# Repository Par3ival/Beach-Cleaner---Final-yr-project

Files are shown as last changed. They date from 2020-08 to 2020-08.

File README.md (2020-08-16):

# Beach-Cleaner---Final-yr-project

This documents all the work put towards the final year group project (6 People).

I ended up doing all the work towards: machine vision, machine learning, creating neural nets, ROS, inter robot communication techniques, message formats, prototype/final product CAD designs and small scale PCB designs.
The rest of the work was mostly worked on by 3 of my team mates: Oly Pope, Jack White and Stephen Jeranyama. With Leo Garroch contributing to LED sequence detection.

THIS IS A CLONED REPO OF ALL WORK CARRIED OUT.

For access to the full Catkin_WS see this link to Google Drive (GitHub hates me!)

--->[ROS BUILD - HOSTED ON DRIVE](https://drive.google.com/drive/folders/1dpi-4POSFZ2x0RheGSwLuPaQL2tJi76T?usp=sharing)<---

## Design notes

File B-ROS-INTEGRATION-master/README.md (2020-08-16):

# B-ROS-INTEGRATION

https://github.com/tue-robotics/cb_base_navigation
`--- Example for nav stack use ---`

https://github.com/abhineet123/ORB_SLAM2 
`--- Example for 2D map for ORBSLAM ---`
# SETTING UP NEW CAMERAS FOR STEREO
This includes if cameras arent changed but their separation is

``rosrun camera_calibration cameracalibrator.py --approximate 1 --size 6x4 --square 0.12 right:=/cam_R/usb_camR/image_raw left:=/cam_L/usb_camL/image_raw left_camera:=/cam_L/usb_camL right_camera:=/cam_R/usb_camR``

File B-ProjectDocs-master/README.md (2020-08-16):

# B-ProjectDocs

#### This repository will demonstrate the design and implemention of a system capable of fulfilling autonomous navigation of a beach and cleaning plastics.  

## Key links  

* [The Buoys Portfolio](https://thebeachbuoys.wordpress.com)

* [ROS Intergration](https://github.com/lboroWMEME-19WSD001/B-ROS-INTEGRATION)

* [CAD designs](https://github.com/lboroWMEME-19WSD001/B-CAD/tree/master/DESIGNS)

* [Idea testing](https://github.com/lboroWMEME-19WSD001/B-Idea-Testing)

* [Identify recycling bins from optically coded sensors](https://github.com/lboroWMEME-19WSD001/B-Idea-Testing/tree/master/LedDetecting)

* [Identify different types of rubbish](https://github.com/lboroWMEME-19WSD001/B-Idea-Testing/tree/master/Deep%20Learning)

* [Identify and alert operators about other wildlife](https://github.com/lboroWMEME-19WSD001/B-ProjectDocs/tree/master/Wildlife%20Alert)

* [Identify waterline and actively avoid or mitigate against the incoming tide](https://github.com/lboroWMEME-19WSD001/B-Idea-Testing/tree/master/Tide_Detection)

## File structure 
**Folders:** Example-Folder

**Files:** example-file

**Read me files:** README.md

The only file in B-ProjectDocs should be README.md, the rest should be folders.

Comments when committing in description box: "+" for changes added "-" for changes removed.

e.g. + added file structure changes

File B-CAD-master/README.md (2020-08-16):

# B-CAD
All cad designs for modelling and printing

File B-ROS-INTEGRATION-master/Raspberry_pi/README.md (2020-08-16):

# Information on coding a Rapberry Pi will go here

## Downloading libraries
Downloading pip: `$ sudo apt install python-pip`

Downlaoding packages: `$ pip install [library name]` 

Check the package is available [here](https://pypi.org/)

## GPIO pinout
https://www.raspberrypi.org/documentation/usage/gpio/

## ROS_SPI and bb_SPI

These two programs were created in conjunction with oneanother to allow for the communication between a raspberry Pi and botboarduino/arduino. This has allowed for full remote control through ROS by subscribing to a topic on the PI, mapping the data and then transmitting over SPI for the aruduino (SPI slave) to recieve and then interpret to turn into movement commands.

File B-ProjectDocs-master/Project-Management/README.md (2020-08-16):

# Weekly tasks will be assigned here 

## 10/02/2020

**Leo:** make some mbed code for actual bin patterns, then video it

## 03/02/2020

**Leo:** Make progress on bin detection code for monday

## 27/01/20

**Oly:** Labview and ROS intergration.

**Dan:** Navigation.

**Jack:** Design tri track top and bottom plate.

**Stephen:** Create a subscriber for Arduio wifi data recieveing (UDP).

**Leo:** Tide detection.

**Iffy:** Continue with mapping.

## 20/01/20

**Jack:** Design a top for the tri track for all the electronics and create a data processing flow chart.

**Dan:** Work on navigation for the robot.

**Leo:** Map for what messages are bring sent.

**Iffy:** Continue with mapping.

**Stephen:** Create a subscriber for Arduio wifi data recieveing (UDP).

## 07/01/20
**Leo:** Produce 20s Vid of code development, continue to develop tide detection technology

**Jack:** Produce 20s Vid of arm development, edit GW2 video and continue to improve collection technology

**Stephen:** Produce 20s Vid of code development, continue to assess integration between ROS and sub-systems

**Oly:** Produce 20s Vid of code development, continue to improve sound response system and complete plan on page

**Ify:** Produce 20s Vid of code development, continue to develop path finding work

**Dan:** Produce 20s Vid of code development, continue work on template matching

## 02/12/19
**Leo:** Tide detection: sensor eval/research, for arduino.

**Jack:** Put holes in lazer cut wood and continue to build arm. Design mounting for cameras and arduino for eye in the sky.

**Stephen:** Global timer for ROS, create a subscriber to get co-ordinates.

**Oly:** Photogramatory for myrio FPGA + seagull sounds + look at labview/ROS intergration

**Ify:** Route planning.

**Dan:** Psudo code for crab tracking and PCB for power supply.

## 25/11/19

**Leo:** Tide detection: sensor eval/research, for arduino.

**Jack:** Put holes in lazer cut wood and continue to build arm. Design mounting for cameras and arduino for eye in the sky.

**Stephen:** Global timer for ROS, create a subscriber to get co-ordinates.

**Oly:** Photogramatory for myrio FPGA + seagull sounds + look at labview/ROS intergration

**Ify:** Route planning.

**Dan:** Psudo code for crab tracking and PCB for power supply.

## 18/11/19

**Dan:** Psudo code for crab tracking and PCB for power supply.

**Oly:** Photogramatory for myrio FPGA + seagull sounds.

**Stephen:** Global timer for ROS, create a subscriber to get co-ordinates and Gazebo.

**Ify:** Route planning.

**Leo:** Identify coloured lights in a video and send data to analyse.

**Jack:** Servo arm and camera mounts.

## 11/11/19

**Leo:** Formatting data to compare with pattern data and write pattern data.

**Jack:** 

stage 1: design arm for robot and draw on CAD.

stage 2: build robot arm and mount to rover.

stage 3: integrate with microcontroller and get bot to work.

**Oly:** Myrio experiments.

**Stephen:** Setting up nodes for ROS and node diagram.

**Ify:** Route planning.

## 04/11/19 - 11/11/19

**Jack:** Designing robot arm and drawing in CAD 

**Leo:** LED indentifying code to work with video and pattern recognition.

**Stephen:** ROS node map.

**Dan:** Machine visin for tracking crabs.

**Oly:** How to detect seagull sound with labVIEW, prepare documents for PST, LabView with myRio.

## 28/10/19 - 04/11/19

**Dan + Leo:** Research on wireless communication, and wireless adapters.

**Leo:** Function to identify LEDs from a picture in simulink or python.

**Stephen + Jack:** ROS.

**Stephen + Oly:**  How to filter microplastics.

**Ify:** LabVEIW.

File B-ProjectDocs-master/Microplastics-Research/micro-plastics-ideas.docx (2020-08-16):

# Requirements

- Filter micro plastics larger than sand
- Automated robot system
- Keep track of areas where sand has been collected
- Collect sand underwater? Adds, complexity

# Filtering techniques

- Electrostatic mesh - https://youtu.be/00Qw36ooUp4
  - https://youtu.be/nfMGrq8W5rI
- Moving mesh filter - https://youtu.be/sHnqjKwVND0

# Robot ideas

- Mini excavators - https://youtu.be/FQZZBF3viI4
  - https://youtu.be/69Gaw0k65qQ
  - https://youtu.be/j4845zwMVBs
- Underwater robot - https://youtu.be/6pBH-3lXXO0

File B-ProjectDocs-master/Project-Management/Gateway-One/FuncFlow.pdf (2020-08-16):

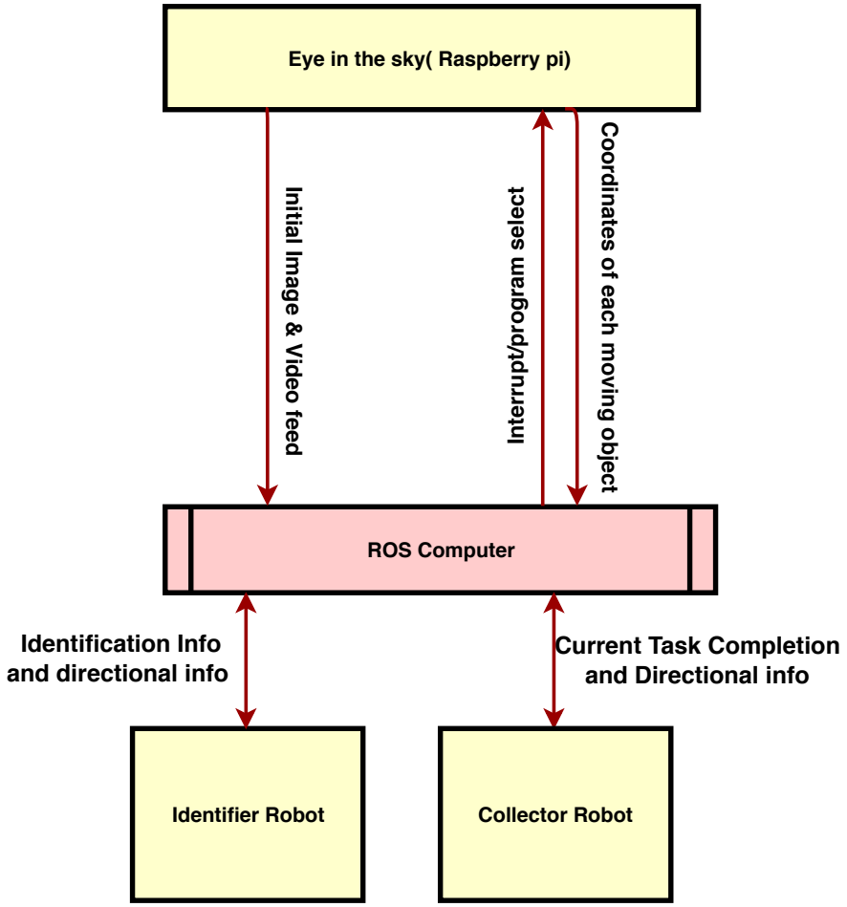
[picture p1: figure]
Eye in the sky( Raspberry pi); ROS Computer; Interrupt/program select; Coordinates of each moving object; Identification Info and directional info; Current Task Completion and Directional info; Collector Robot

# Identifier Robot Initial Image & Video feed

# Flow Diagram of the Main Idea

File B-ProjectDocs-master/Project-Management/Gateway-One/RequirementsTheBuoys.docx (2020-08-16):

# Group Project Systems Approach

# Introduction

Aim: Utilise integrated autonomous technologies to enhance and develop waste management in coastal areas

Objectives:

- Integration of several individual systems to produce a more complex system of systems, capable of delivering user specified tasks
- Automation of whole system to minimise human interactions
- Effective and comprehensive movement of different materials to specified areas

# Requirements Specification

## Navigation and mapping

Description

The system will map objects’ locations and the position of the tide. This information will be used to task sub-systems and determine routes for them to travel.

Stimulus/Response Sequences

Objects on the surface will be detected and their coordinates noted. A sub system will then receive these coordinates and move to that position, avoiding any potential hazards. This process will be utilized again when the type of material has been determined and the sub system will move to its designated bin.

Functional Requirements

NM_REQ_1: System must detect all objects within the designated area

NM_REQ_2: System must build database of all objects’ coordinate locations

NM_REQ_3: System should send coordinates to specific sub system

NM_REQ_4: Sub system should path find to designated coordinates without interfering with other hazards or objects

## Identification and sorting

Description

The system should be able to differentiate between types of materials and tag them appropriately.

Stimulus/Response Sequences

A series of LEDs will be identified by the system and bin type deciphered. Objects found within the designated area will have their type determined and this be tagged for further processing.

Functional Requirements

IS_REQ_1: System must decode series of lights

IS_REQ_2: System must determine types of objects due to material made of

## Wildlife mitigation

Description

The system should be able to detect different wildlife in the locale and react appropriately.

Stimulus/Response Sequences

Crabs will be detected by the system and their paths tracked. Seagull noises will be acoustically recognised, prompting an appropriate response.

Functional Requirements

WM_REQ_1: System will identify when in presence of wildlife

WM_REQ_2: System should track movements of wildlife when appropriate

WM_REQ_3: System will conduct mitigation procedure when wildlife detected

## Collection and delivery

Description

The system will pick up and collect various objects from the designated area and deposit them to a pre-determined location.

Stimulus/Response Sequences

Upon arrival at an objects location, the system will attempt to pick up said object before moving to the coordinates of its corresponding bin. Here the system will release the object before waiting for new tasking.

Functional Requirements

CD_REQ_1: System will acquire and pick up an object from a specified location

CD_REQ_2: System will deposit object after arrival at specified location.

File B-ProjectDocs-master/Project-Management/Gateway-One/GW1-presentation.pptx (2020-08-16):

## GW1

The Buoys

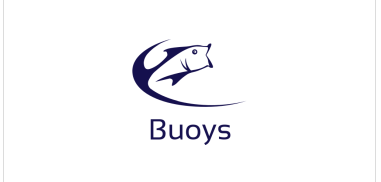
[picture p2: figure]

## Team structure

Stephen – Project Manager + Software Assist
Oly – Management Assist + Integration
Ify – Integration
Jack – Design + Integration
Dan – Machine Vision
Leo – Machine Vision

## requirements

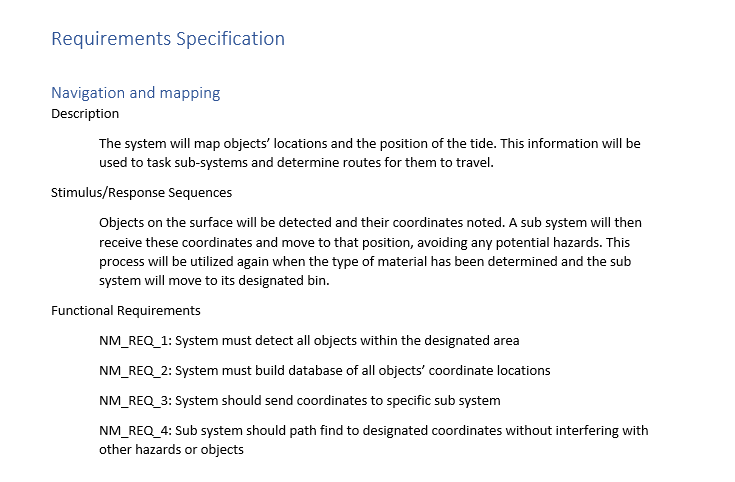
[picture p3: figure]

## Functional flow

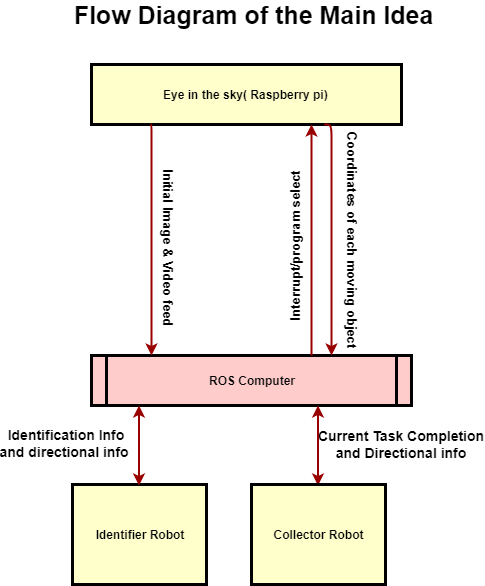
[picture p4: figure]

## Project Management

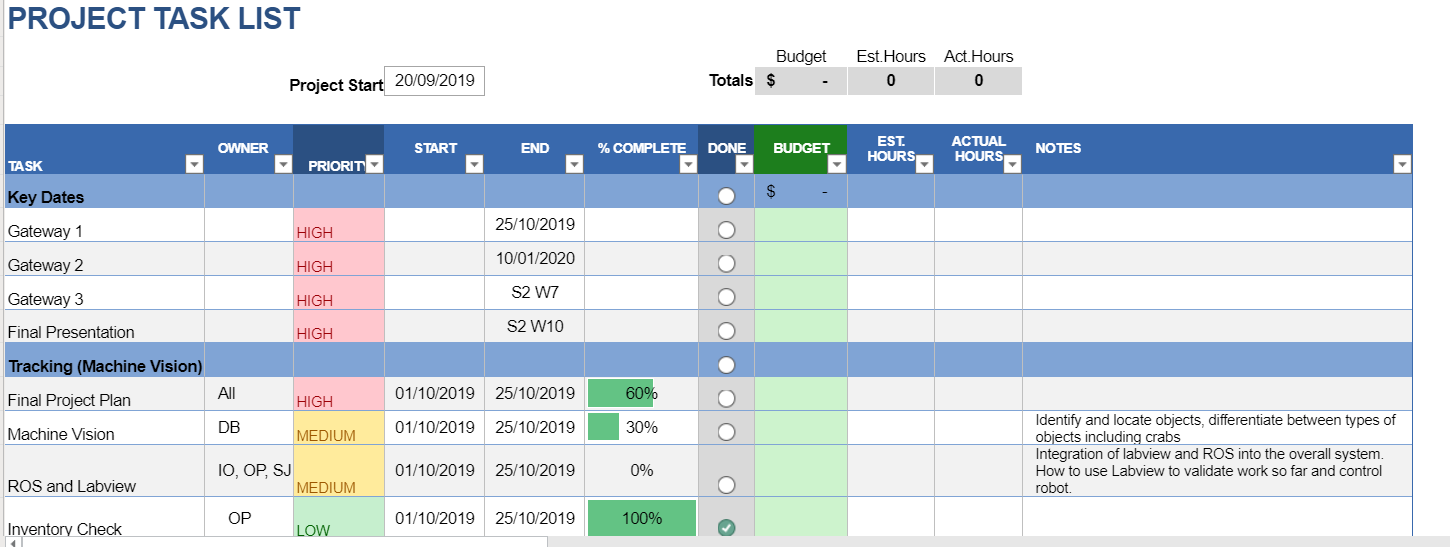
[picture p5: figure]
A screenshot of a video game Description generated with high confidence
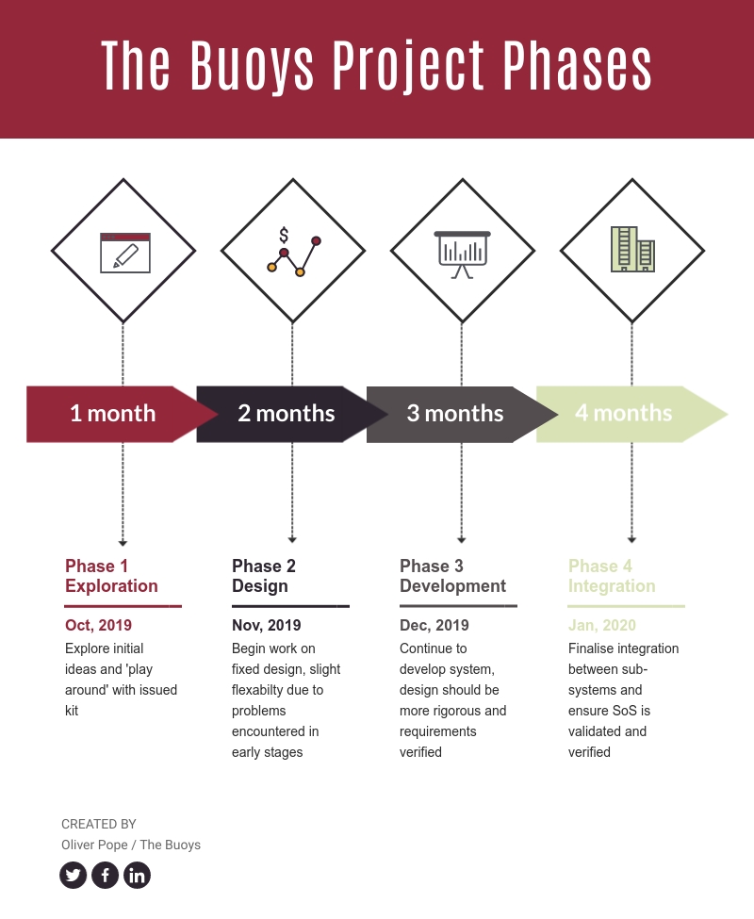
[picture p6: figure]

## Critical Evaluation

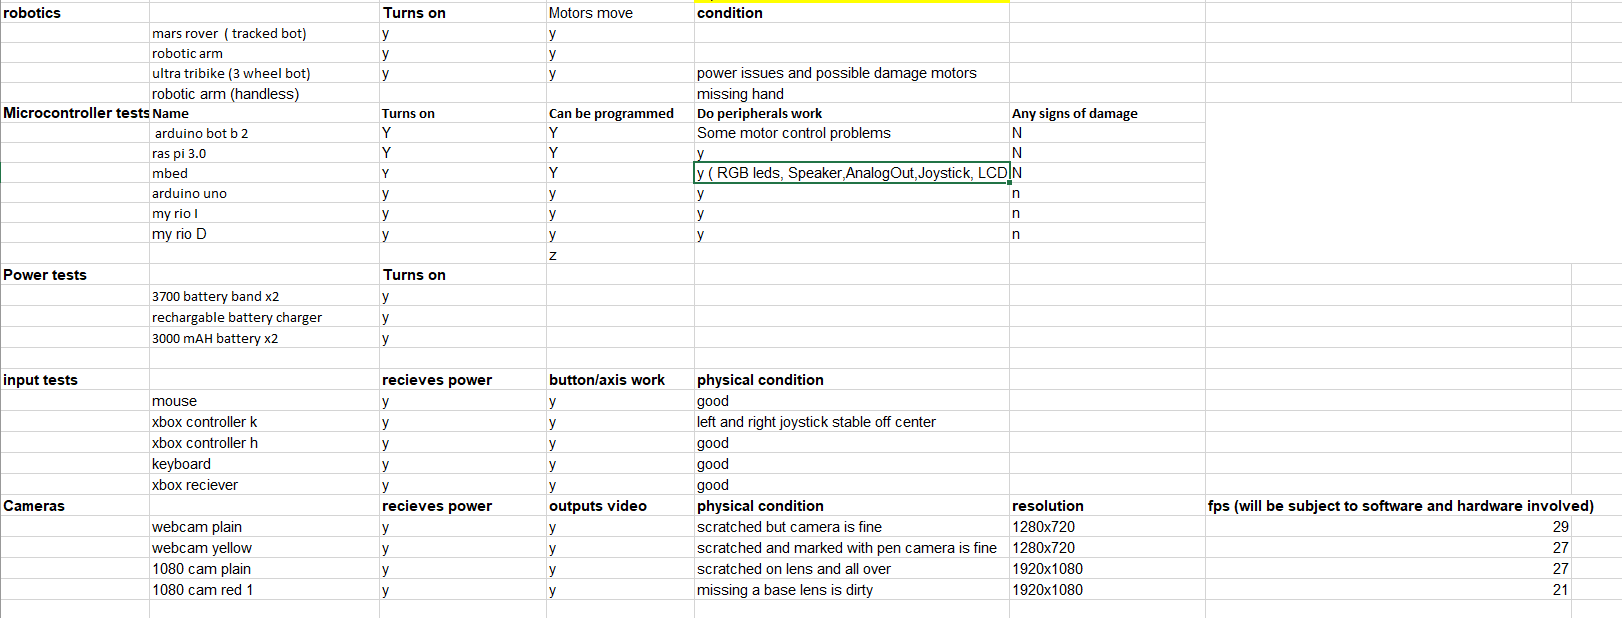
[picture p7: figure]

## Technical Research – Machine vision

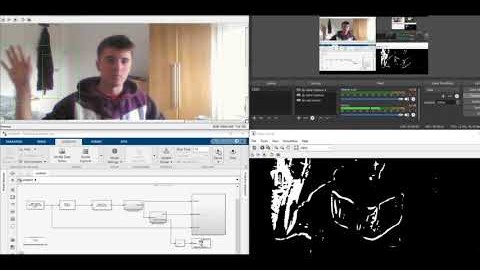
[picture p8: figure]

## Technical Research – Wireless control

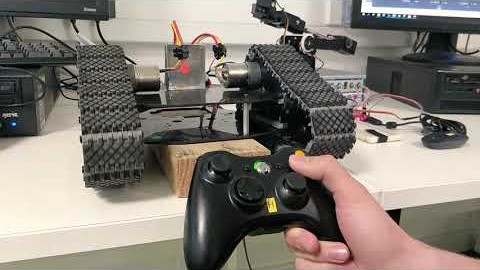
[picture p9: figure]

## Version Control

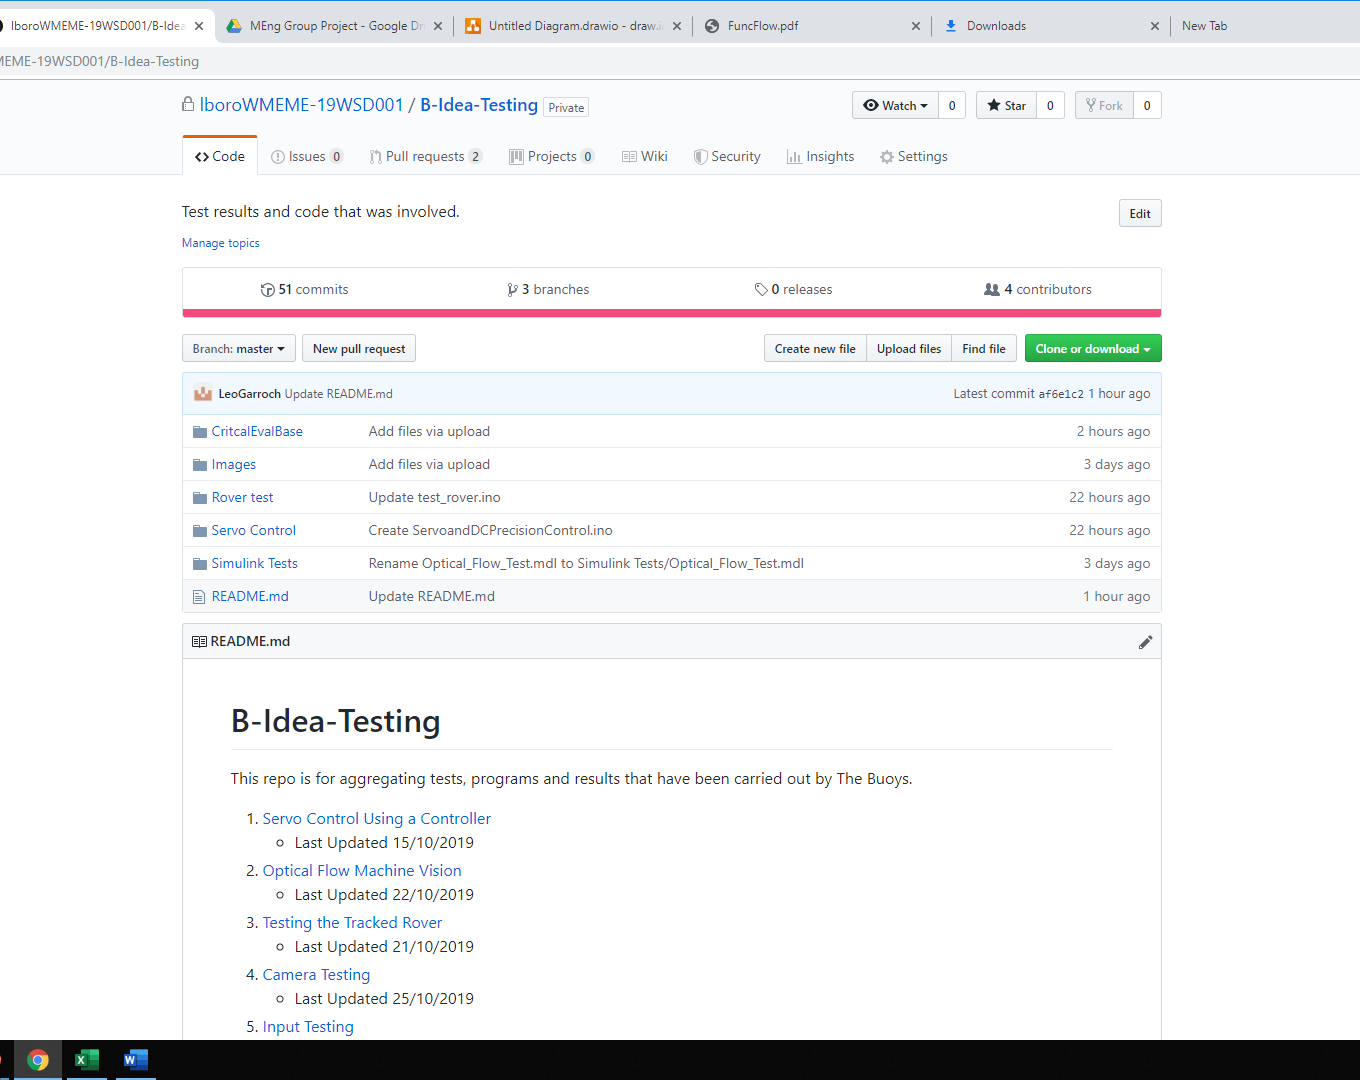
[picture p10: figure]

## 19WSD001 Team Project

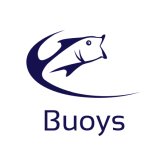
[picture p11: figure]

23/10/19

AIMS & OBJECTIVES
Aim: Utilise integrated autonomous technologies to enhance and develop waste management in coastal areas.
Objectives: Integration of several individual systems to produce a more complex system of systems, capable of delivering user specified tasks.
Automation of whole system to minimise human interactions
Effective and comprehensive movement of different materials to specified areas

Activities

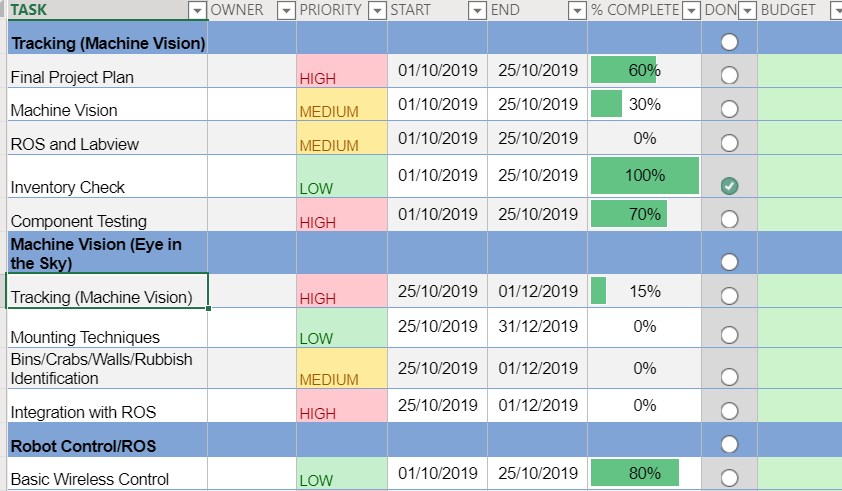
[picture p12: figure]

Budget statement
Current budget at £200, no immediate spending forecast.

Stakeholders
P: Environment Secretary, Local Councils
E: Private Investors, Gov’t grants, PST (Budget Approval)
S: Users, Media, Charities, Environmentalists, Public
T: PST, Researchers, Hard/Software developers
L: Environment Agency, Gov’t
E: Gov’t, Environmental organisations

Mission phase completion
4 main phases; completed exploration phase now onto design. Have tested components and researched varying ideas and now moving onto a more rigorous design although remaining pragmatic to counter potential issues during continued development of project.

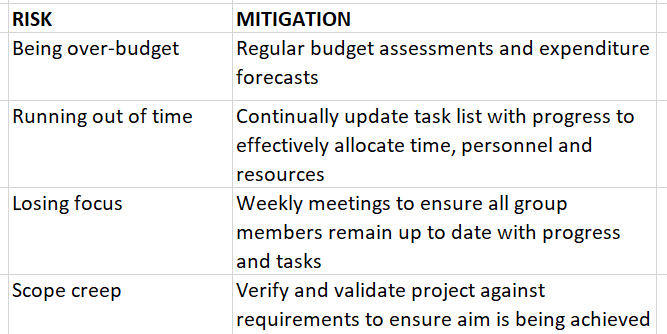
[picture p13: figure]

Key issues and risks

The Buoys
https://lunet-my.sharepoint.com/:f:/r/personal/elop4_lunet_lboro_ac_uk/Documents/MEng%20Group%20Project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

Strategy/ Plan
Exploration: Explore initial ideas and ‘play around’ with issued kit.
Design: Begin work on fixed design, slight flexibility due to likelihood of problems encountered in early stages
Development: Continue to develop system, design should be more rigorous, and requirements verified
Integration: Finalise integration between sub-systems and ensure SoS is validated and verified. System will be fully autonomous

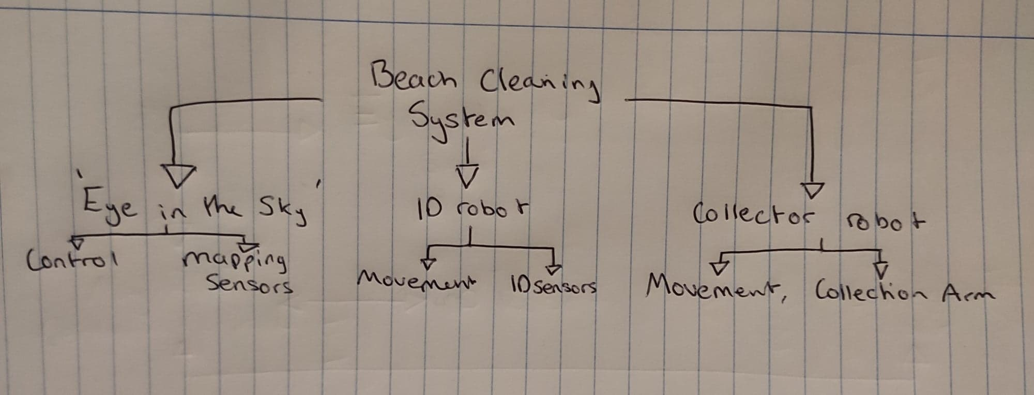
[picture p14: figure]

Programme

GW1

GW2

GW3

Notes: A version of this is compulsory at each gateway meeting and optional for PST meetings.
In terms of sizing, this should be legible printed on A3, but will probably be viewed on screen. Minimum font size =12
Diagram in the middle should be a top level systems diagram.
The plan will change as the project progresses – that is ok and expected.

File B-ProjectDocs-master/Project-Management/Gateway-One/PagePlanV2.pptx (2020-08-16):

## 19WSD001 Team Project

[DATE]

Aim: Utilise integrated autonomous technologies to enhance and develop waste management in coastal areas.
Objectives: Integration of several individual systems to produce a more complex system of systems, capable of delivering user specified tasks.
Automation of whole system to minimise human interactions,
effective and comprehensive movement of different materials to specified areas

Activities (How)
Including status (with key). Will need to be clear as to the time period under consideration.

Budget statement
Current budget at £200, no immediate spending forecast.

Stakeholders (Who?)
PST, Legislators,

Mission phase completion
4 main phases; completed exploration phase now onto design. Have tested components and researched varying ideas and now moving onto a more rigorous design, although remaining pragmatic to counter potential issues during continued development of project.

Strategy/ Plan (Why?)

Key issues and risks
Stay within time and budget.
Maintain focus.
Maintain Communication

Team information
Name, logo, link to portfolio, link to Gihub
The Buoys

Programme

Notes: A version of this is compulsory at each gateway meeting and optional for PST meetings.
In terms of sizing, this should be legible printed on A3, but will probably be viewed on screen. Minimum font size =12
Diagram in the middle should be a top level systems diagram.
The plan will change as the project progresses – that is ok and expected.

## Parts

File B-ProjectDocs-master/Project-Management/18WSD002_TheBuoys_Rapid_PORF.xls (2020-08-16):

Requisition No:
PURCHASE ORDER REQUEST FORM
Please order the following Goods/Services from: (If tenders are required, contact Purchasing Office)
Company Name:
Contact:
Address:
www.
E-mail:
Telephone Number:
Fax Number:
 |  |  |  |  | Version February 2017
ITEMS REQUIRED |  |  |  | Where discounts have been negotiated these should be clearly shown below
Description |  |  | Part No. | Quantity | Unit Cost | Total Cost
 |  |  | 73-5280 | 1 | £20.86 | £20.86
 |  |  | 58-2872 | 1 | £26.99 | £26.99
Checked by Health & Safety Officer:
Project code | Product code | Amount | Budget Holder's Signature |  | Discount
WS1407 |  | £57.42 |  |  | Delivery
 |  |  |  |  | Sub-Total | £47.85
 |  |  |  |  | VAT | £9.57
 |  |  |  |  | Total | £57.42
Date: | 2019-11-12 | Name of Requisitioner: | Oliver Pope
 |  | Tel: | 7547687896
 |  | Email: | o.pope2-17@student.lboro.ac.uk
 |  | Signature: | Oliver Pope
AUTHORISATION
DDP/EQUIVALENT______________________________________________________________
Ordered By: ____________________ Date: _____________ Order Number: _________________
Completed Inventory: Yes No Inventory Code: _________________________________

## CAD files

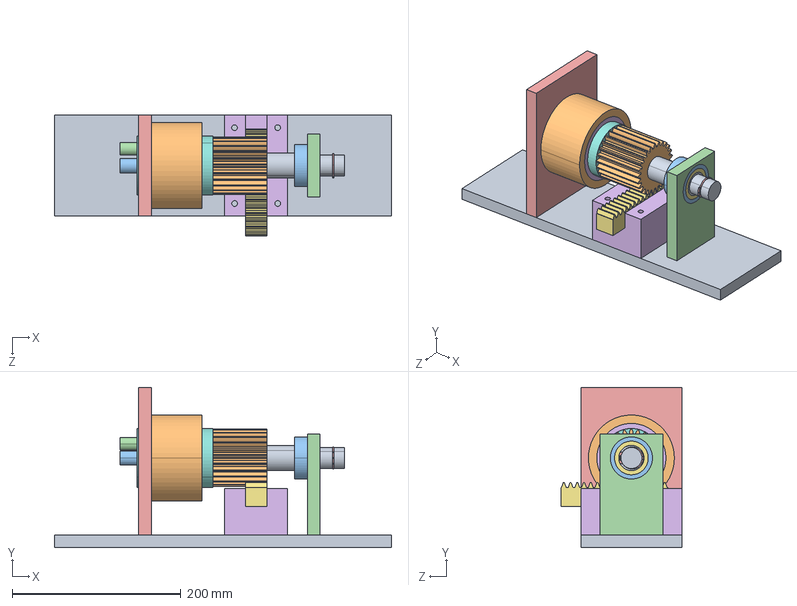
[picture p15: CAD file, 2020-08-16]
B-CAD-master/DESIGNS/Rack pinion assembly.STEP
400.0 x 190.0 x 143.5 mm
base plate
housing
housing 2
housing holder
bush1
bush2
spur gear_ai2_Inch - Spur gear 10DP 25T 20PA 2.52FW ---S25N3.0H2.0L0.03125N
pin 1
pin 2
heavy duty external retaining ring_am_B27.8M - 3DM1-22
cast iron block
rack spur rectangular_ai_Inch - Rack-spur - rectangular 10DP 20PA 1FW 1PH 5L---SAll

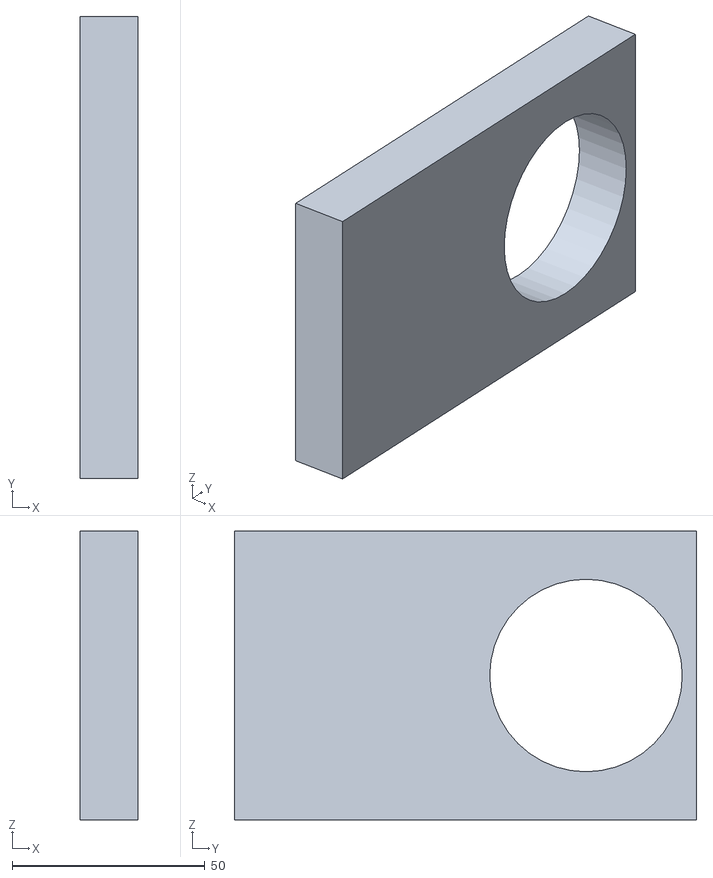
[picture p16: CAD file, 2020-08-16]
B-CAD-master/DESIGNS/Rack pinion assembly_step.stl
15.0 x 120.0 x 75.0

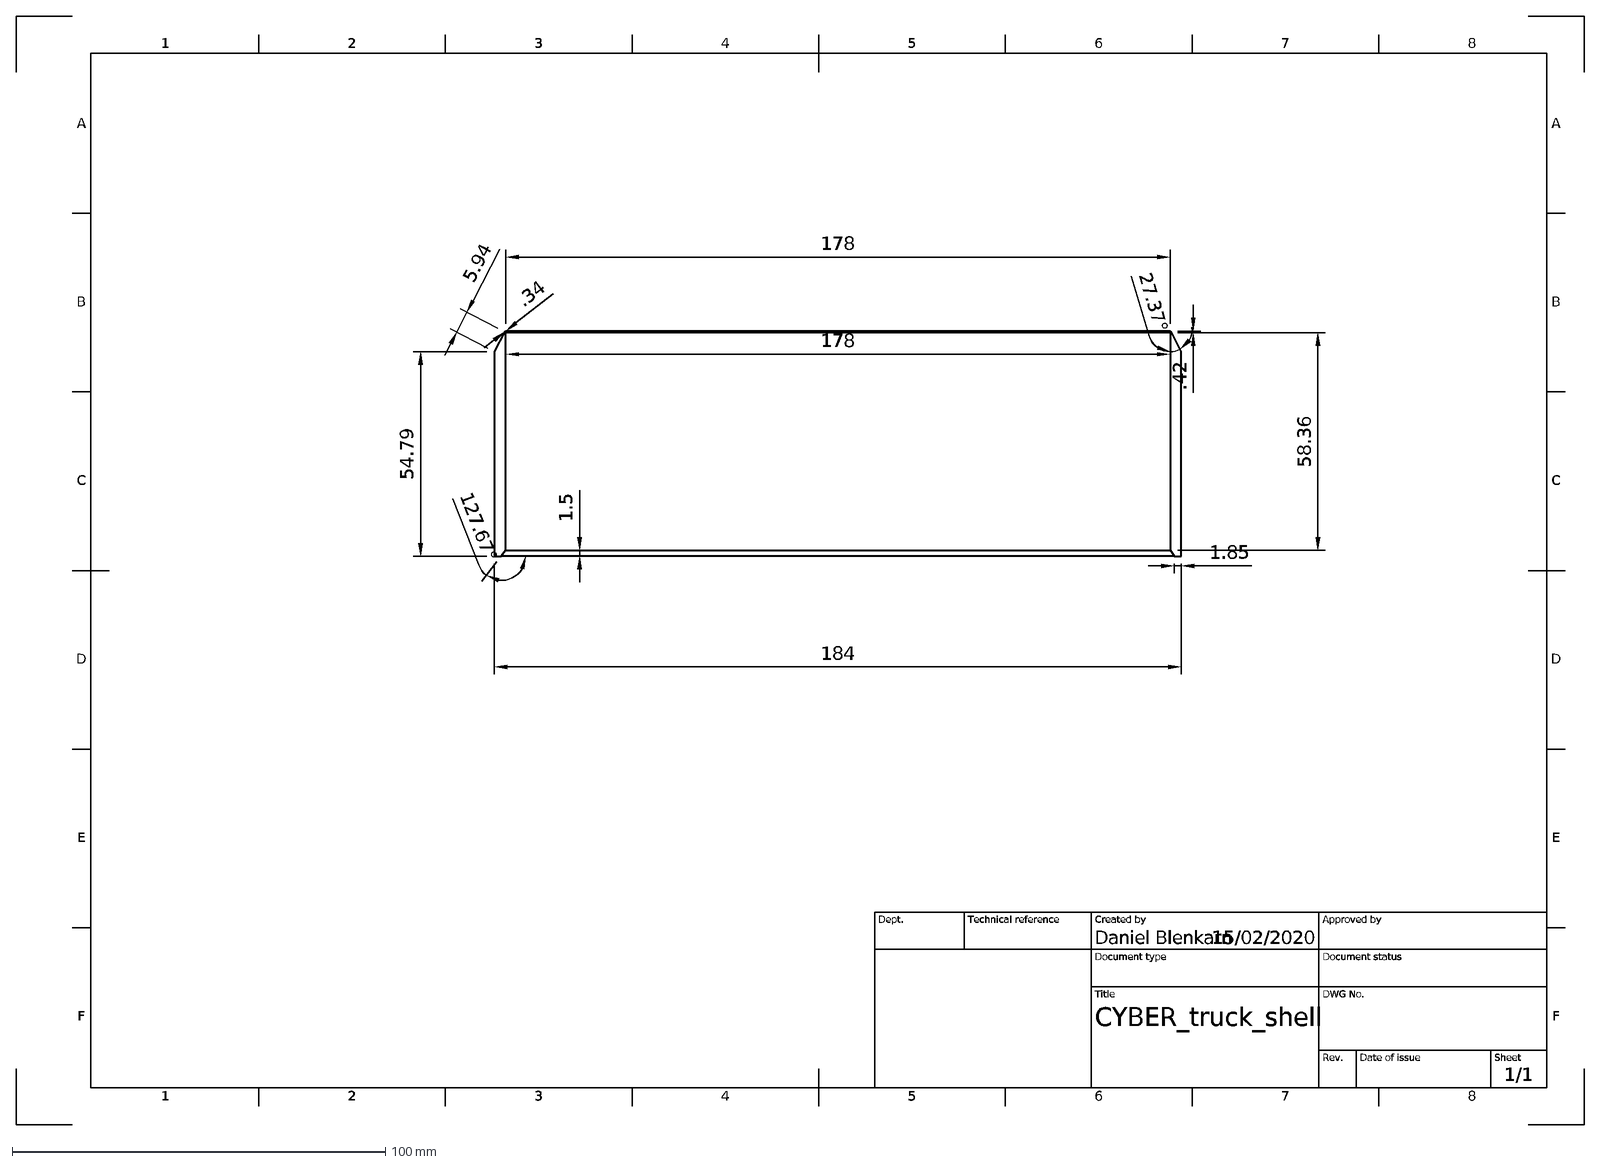
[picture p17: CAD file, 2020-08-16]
B-CAD-master/DXF Output/CYBER_truck_shell Drawing BACK v1 Sheet1.dxf
1
A
2
3
4
5
6
7
8
B
C
D
E
F
15/02/2020
1/1
CYBER_truck_shell
Daniel Blenkarn
Dept.
Technical reference
Created by
Approved by
Document type
Document status
Title
DWG No.
Rev.
Date of issue
Sheet
178
58.36
54.79
184
5.94
.34
.42
1.5
1.85
27.37°
127.67°

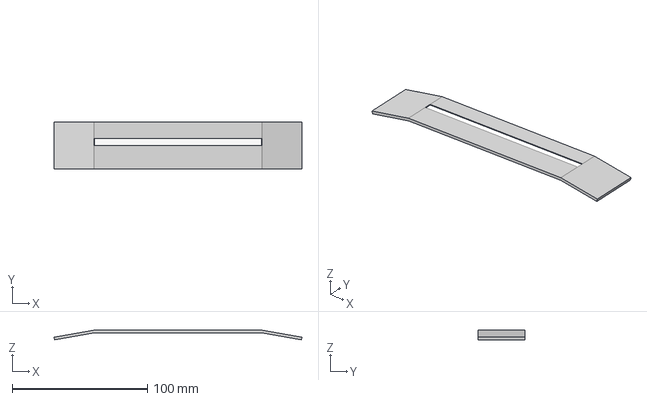
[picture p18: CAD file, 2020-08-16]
B-CAD-master/MOCKUPS/CYBER_truck_front v1.step
183.1 x 35.0 x 7.20 mm

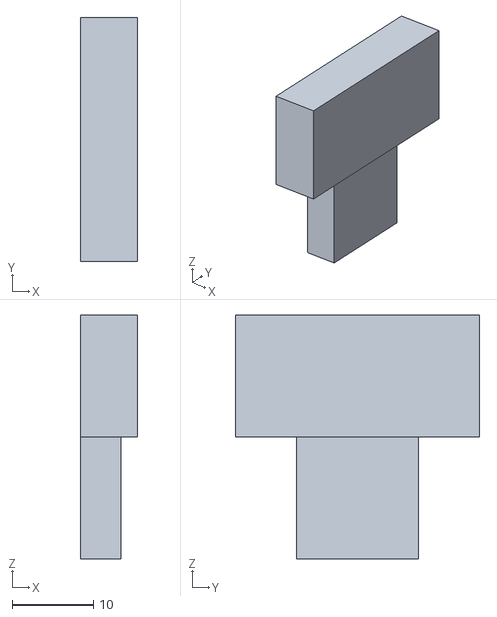
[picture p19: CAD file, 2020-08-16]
B-CAD-master/DESIGNS/cameraholder2.stl
7.00 x 30.0 x 30.0

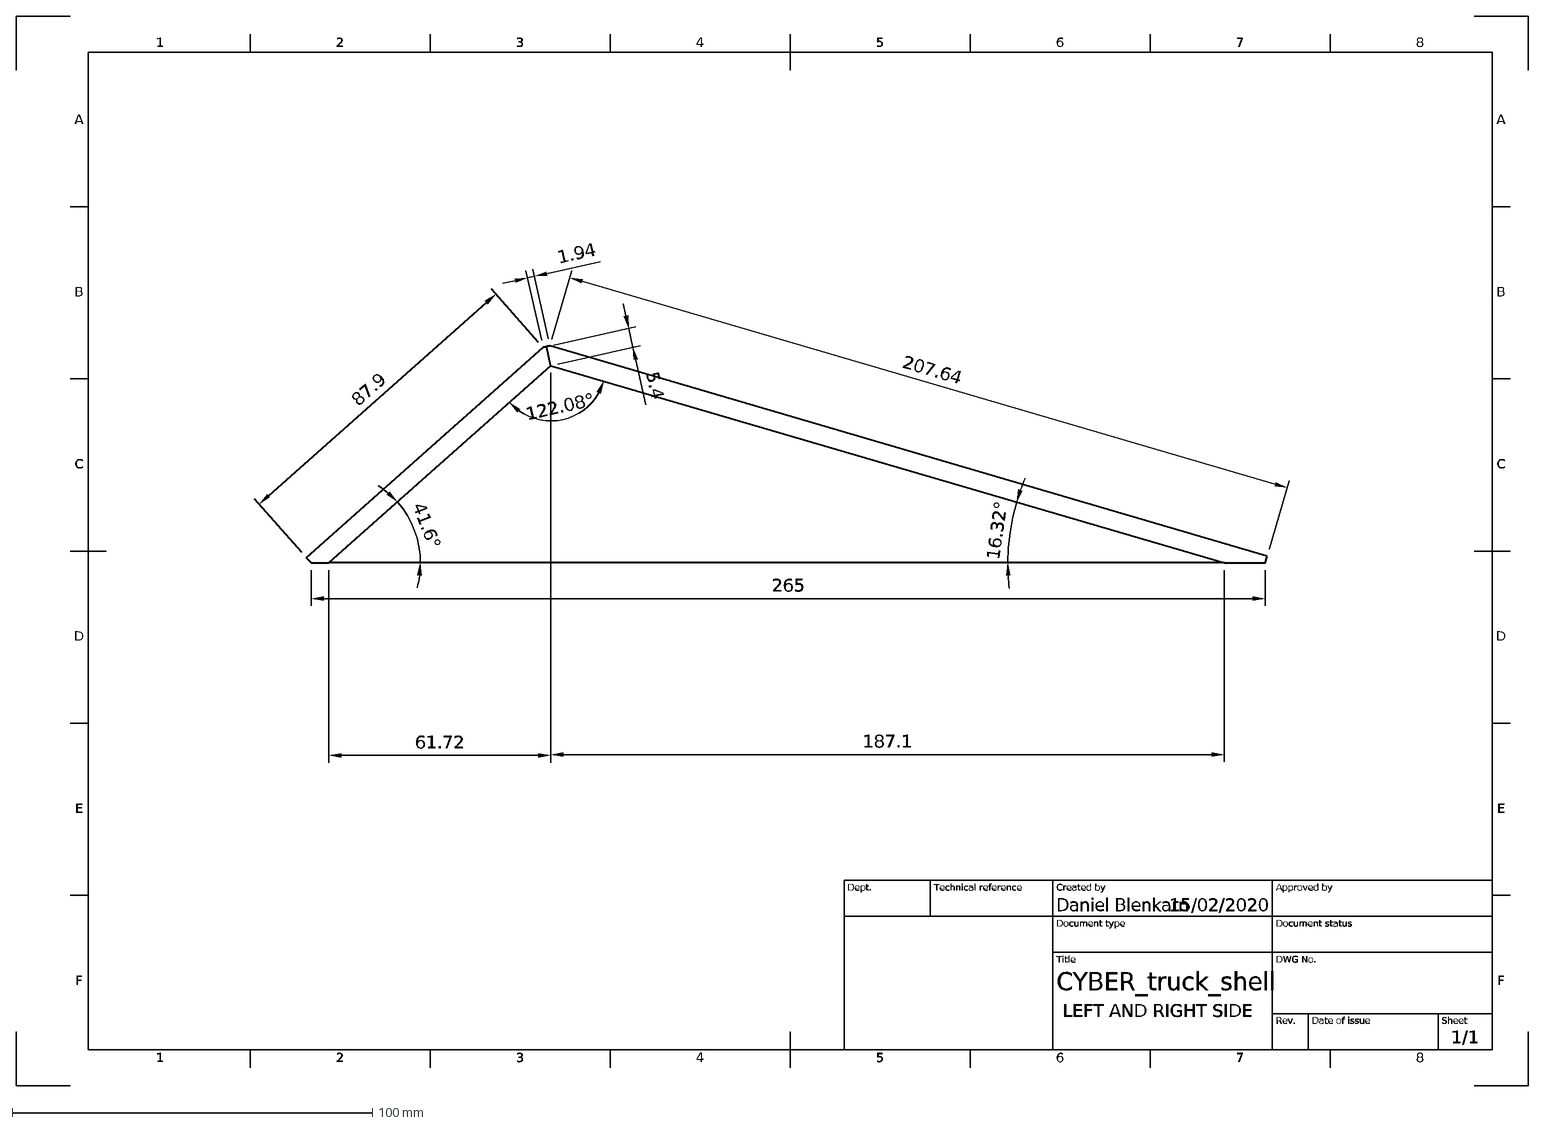
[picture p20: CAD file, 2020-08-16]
B-CAD-master/DXF Output/CYBER_truck_shell Drawing sides v2 Sheet1.dxf
1
A
2
3
4
5
6
7
8
B
C
D
E
F
15/02/2020
1/1
CYBER_truck_shell
Daniel Blenkarn
Dept.
Technical reference
Created by
Approved by
Document type
Document status
Title
DWG No.
Rev.
Date of issue
Sheet
207.64
87.9
1.94
187.1
265
61.72
5.4
LEFT AND RIGHT SIDE
122.08°
41.6°
16.32°

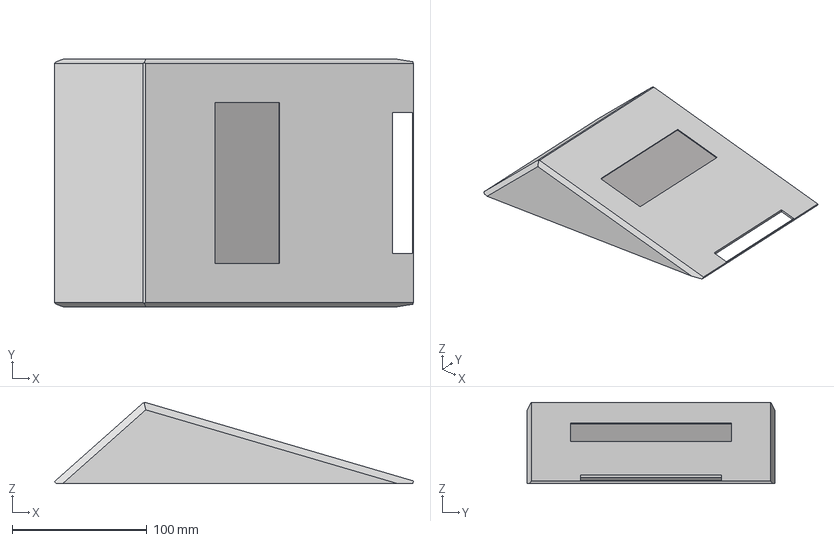
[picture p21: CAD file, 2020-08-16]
B-CAD-master/MOCKUPS/CYBER_truck_shell v4.step
266.9 x 184.0 x 60.3 mm

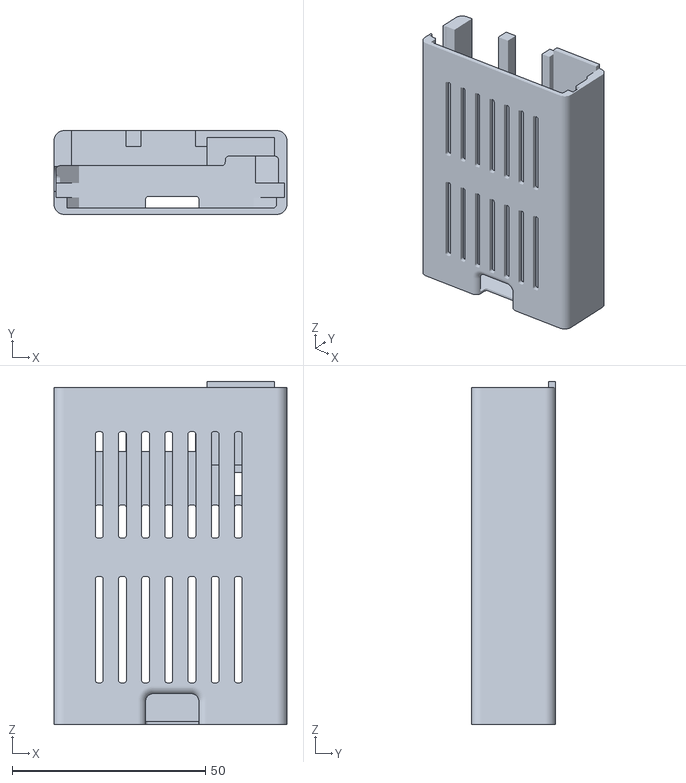
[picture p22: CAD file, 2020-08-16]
B-CAD-master/DESIGNS/Raspberry_PI_4_Sleeve_GPIO_PoE_v6.STL
60.3 x 21.7 x 88.8

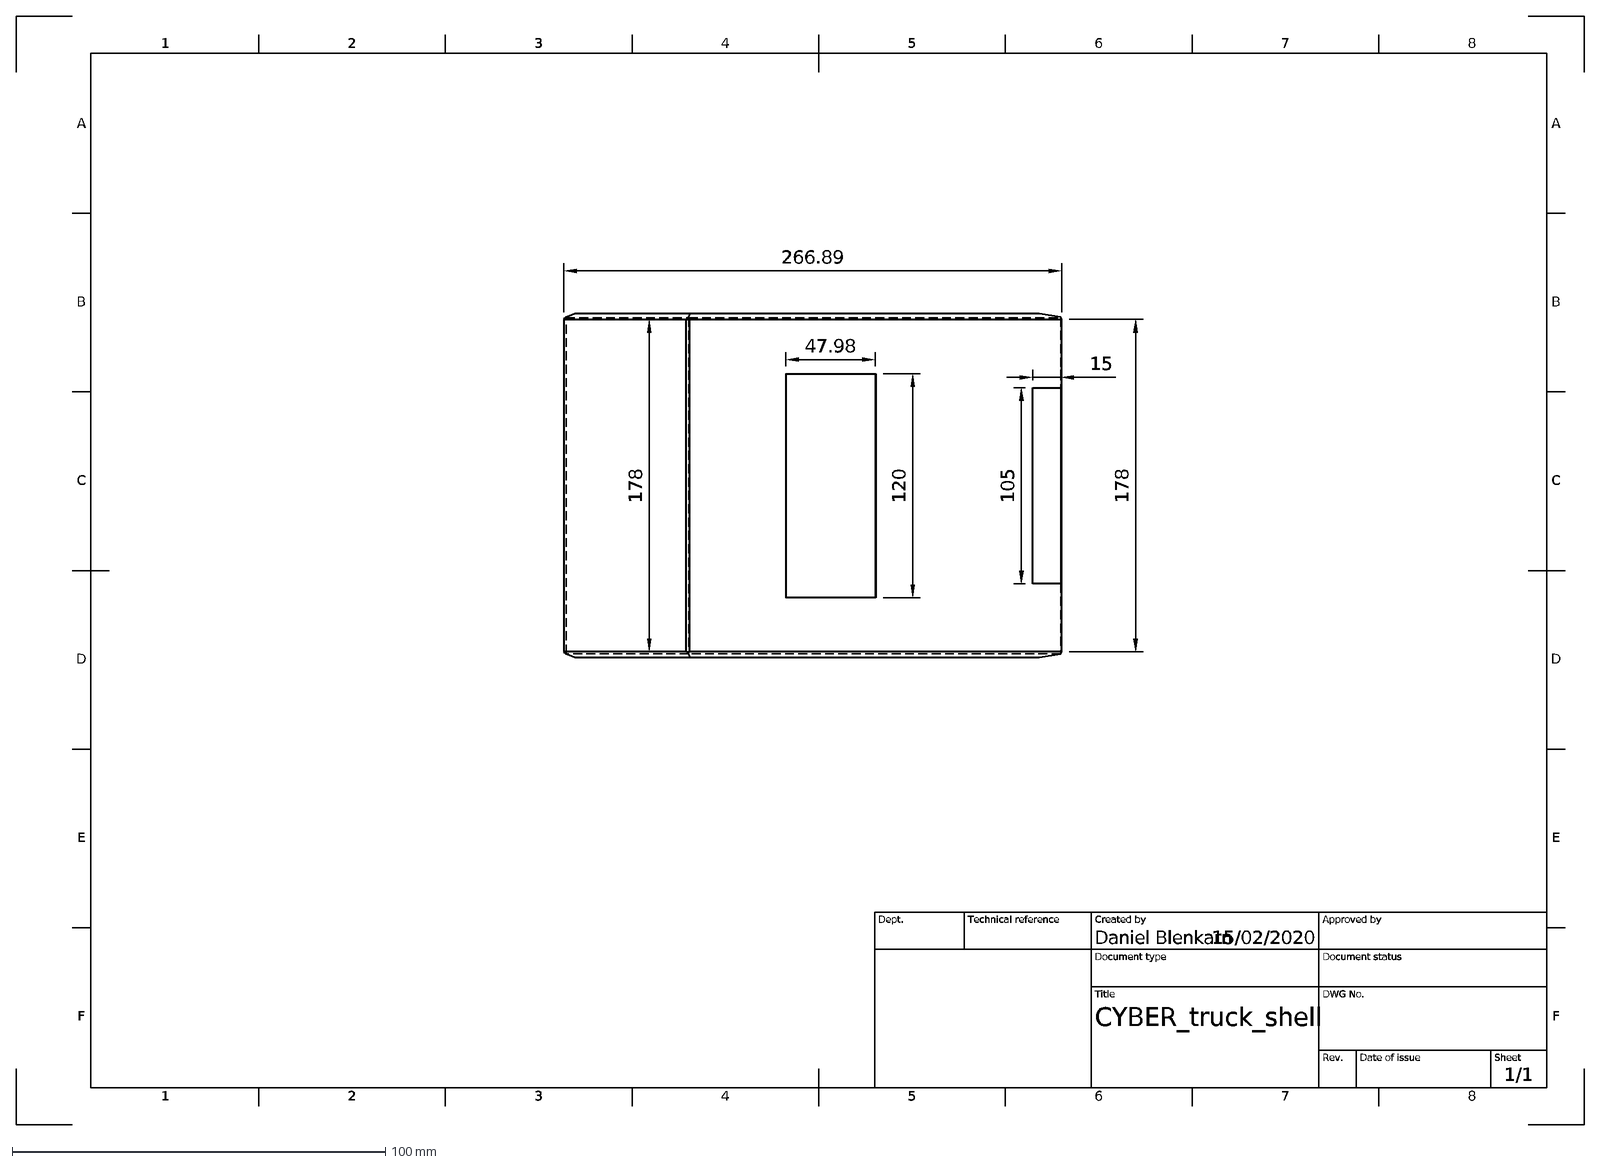
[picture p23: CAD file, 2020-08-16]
B-CAD-master/DXF Output/CYBER_truck_shell top v1 Sheet1.dxf
1
A
2
3
4
5
6
7
8
B
C
D
E
F
15/02/2020
1/1
CYBER_truck_shell
Daniel Blenkarn
Dept.
Technical reference
Created by
Approved by
Document type
Document status
Title
DWG No.
Rev.
Date of issue
Sheet
47.98
120
105
15
178
266.89

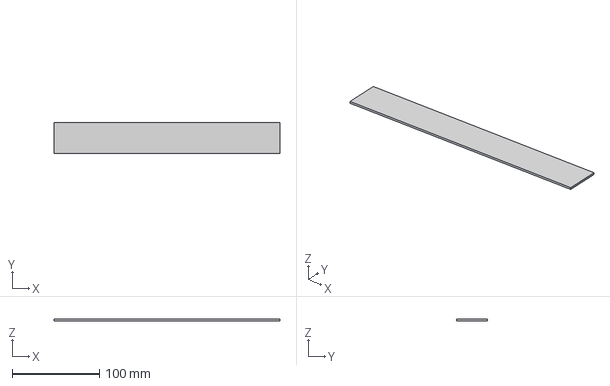
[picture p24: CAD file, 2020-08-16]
B-CAD-master/MOCKUPS/CYBER_truck_side(s) v3.step
259.0 x 35.0 x 2.00 mm

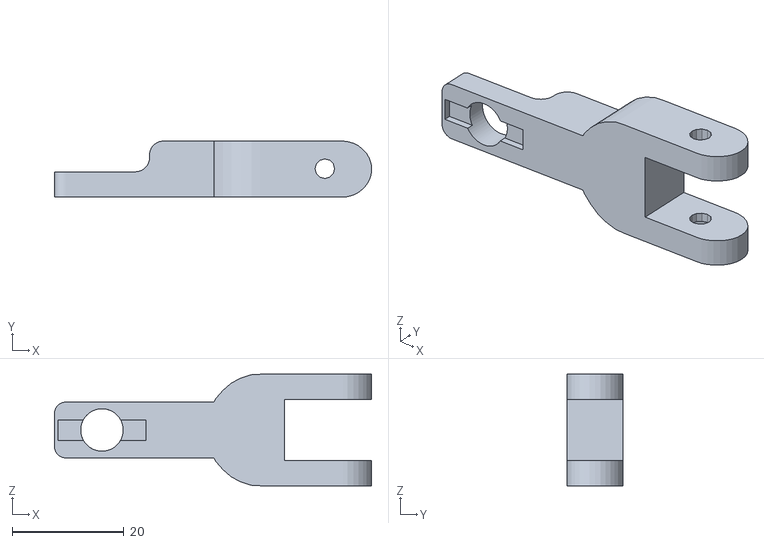
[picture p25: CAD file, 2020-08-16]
B-CAD-master/DESIGNS/F100_Tripod_Holder.stl
56.7 x 10.0 x 20.0

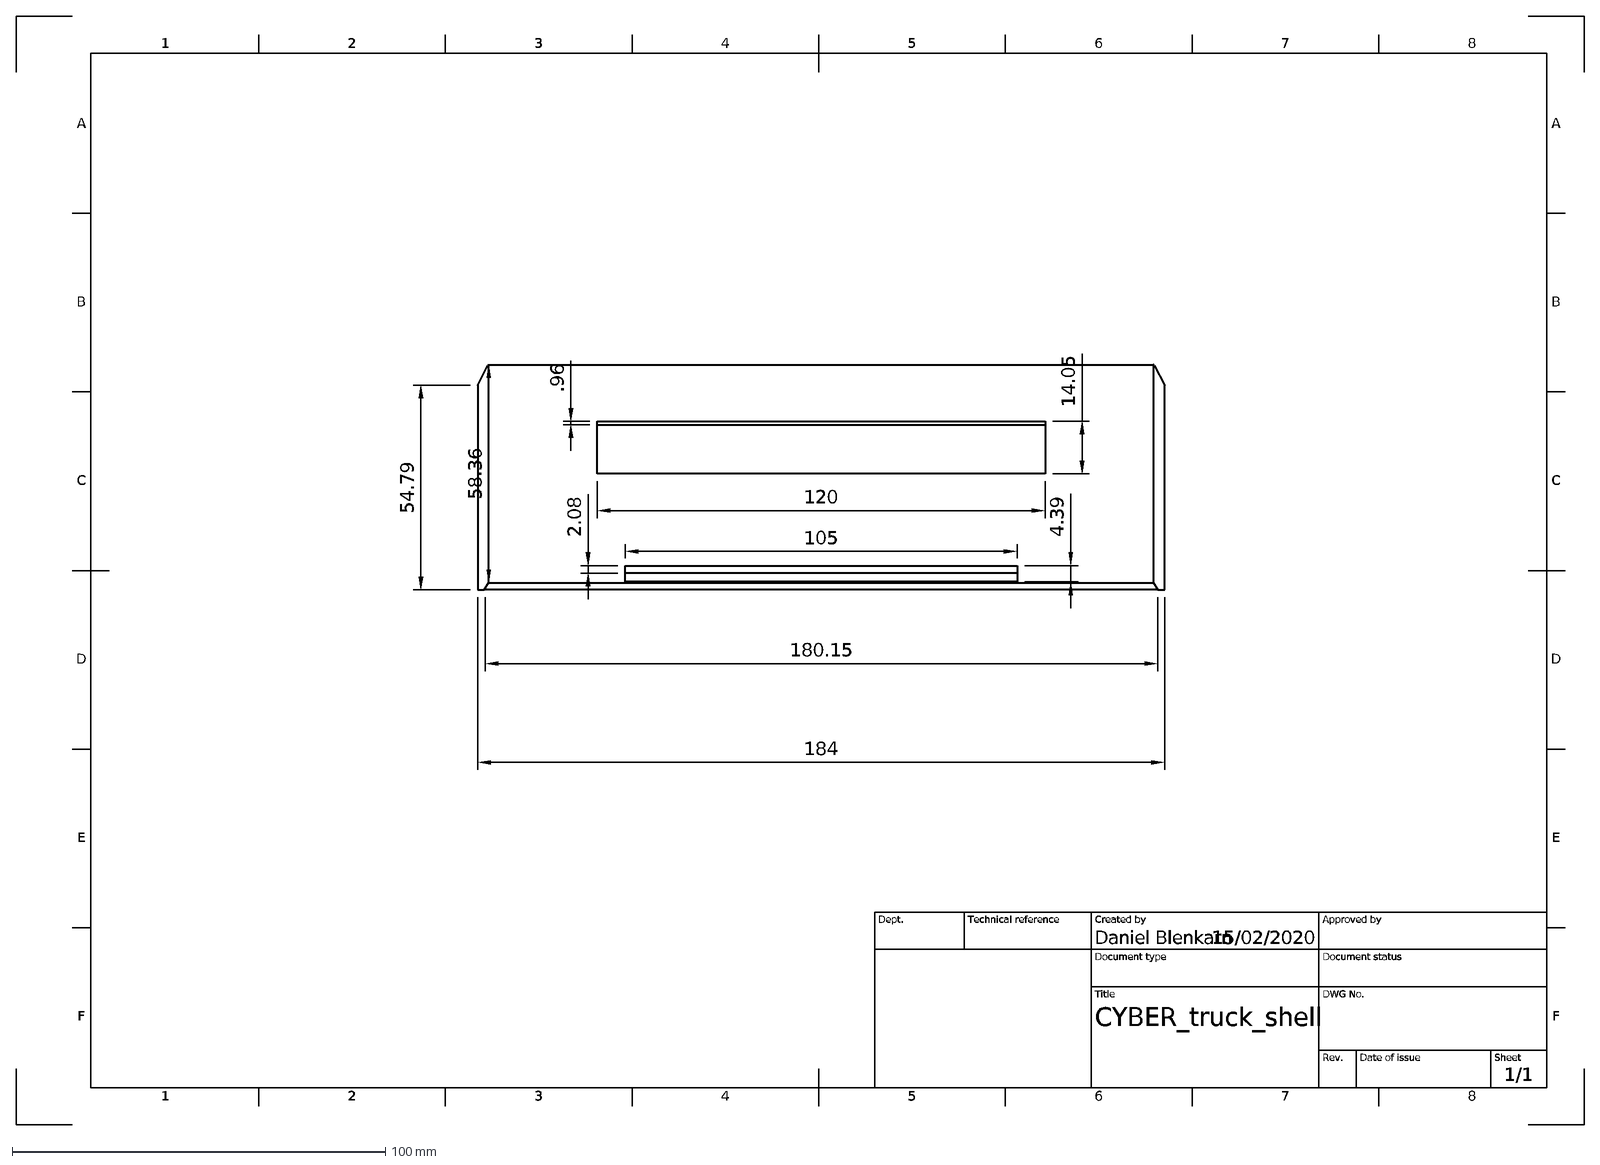
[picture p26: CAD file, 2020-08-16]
B-CAD-master/DXF Output/CYBER_truck_shell Drawing front v1 Sheet1.dxf
1
A
2
3
4
5
6
7
8
B
C
D
E
F
15/02/2020
1/1
CYBER_truck_shell
Daniel Blenkarn
Dept.
Technical reference
Created by
Approved by
Document type
Document status
Title
DWG No.
Rev.
Date of issue
Sheet
.96
120
14.05
2.08
105
4.39
184
180.15
58.36
54.79

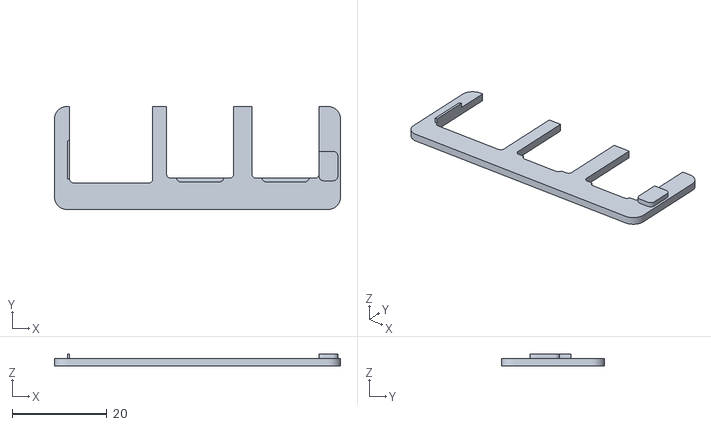
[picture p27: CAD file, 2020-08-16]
B-CAD-master/DESIGNS/Raspberry_PI_4_Sleeve_cap_v4.STL
60.3 x 21.7 x 2.60

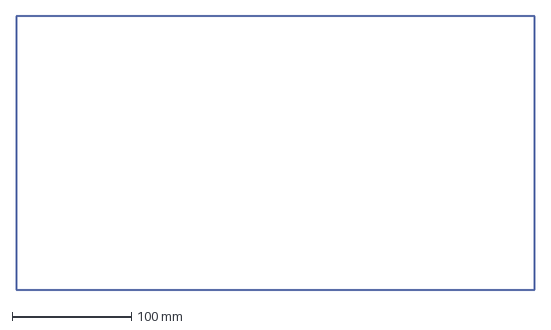
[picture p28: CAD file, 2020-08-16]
B-CAD-master/DESIGNS/robot base mount.dxf
435.0 x 230.0 mm

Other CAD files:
B-CAD-master/MOCKUPS/CYBER_truck_back v1.step
B-CAD-master/DESIGNS/Roverbase.20.dxf
B-CAD-master/DESIGNS/Roverbasebottom.dxf
B-CAD-master/DESIGNS/Arduinopart.prt
B-CAD-master/DESIGNS/Drawing2.prt
B-CAD-master/DESIGNS/Lazer cut drawings.prt
B-CAD-master/DESIGNS/Lazer cut drawings_dwg1.prt
B-CAD-master/DESIGNS/Part1.prt
B-CAD-master/DESIGNS/Part17740.prt
B-CAD-master/DESIGNS/Part2.prt
B-CAD-master/DESIGNS/Part22644.prt
B-CAD-master/DESIGNS/Part8.prt
B-CAD-master/DESIGNS/Part88673.prt
B-CAD-master/DESIGNS/Rack pinion assembly_step.prt
B-CAD-master/DESIGNS/Roverbase.prt
B-CAD-master/DESIGNS/base plate.prt
B-CAD-master/DESIGNS/base plate3694.prt
B-CAD-master/DESIGNS/bush1.prt
B-CAD-master/DESIGNS/bush13838.prt
B-CAD-master/DESIGNS/bush2.prt
B-CAD-master/DESIGNS/bush21025.prt
B-CAD-master/DESIGNS/cameraholder2.prt
B-CAD-master/DESIGNS/cast iron block.prt
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

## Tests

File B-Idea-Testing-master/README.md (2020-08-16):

# B-Idea-Testing

This repo is for aggregating tests, programs and results that have been carried out by The Buoys.

Portfolio can be found here at [The Buoys](https://thebeachbuoys.wordpress.com)!

1. [Servo Control Using a Controller](#3-servo-motors-controlled-wirelessly)
    - Last Updated 15/10/2019
2. [Optical Flow Machine Vision](#simulink--optical-flow-model)
    - Last Updated 22/10/2019
3. [Testing the Tracked Rover](#rovertest)
    - Last Updated 21/10/2019
4. [Camera Testing](#camera-tests)
    - Last Updated 25/10/2019
5. [Input Testing](#inputs-tests)
    - Last Updated 25/10/2019
6. [Mbed Testing](#mbed-testing)
    - Last Updated 25/10/2019
7. [Raspberry Pi Testing](#raspberry-pi-testing)
    - Last Updated 03/12/2019
8. [Neural Networks](#deep-learning)
    - Last Updated 29/10/2019
9. [Arduino Publisher](#blink-led-using-ros)
    - Last Updated 24/11/2019
10. [ROS Websocket Control Page](#ros-webpage-control-with-roslibjs)
    - Last Updated 08/01/2020 
11. [ROS Mono Slam](#ros-mono-slam-with-orbslam2)
    - Last Updated 16/01/2020 

# 3 Servo Motors Controlled Wirelessly

This was a test to confirm that the following was in working order:
- Servo Motors from LynxMotion
- Botboarduino from Lynxmotion
- Sparkfun USB Host Shield
- Xbox 360 Reciever and Controller

After testing it was found that all the components named above were in working order, as of 15/10/2019.
However 2 servos as part of one of the servo arms were non-functional.

[Video demonstration](https://youtu.be/stPPC0m9og8)

**Things to note:**
- Botboarduino cannot provide sufficient current to both the reciever and servos at the same time off the 5v rails.
This was solved by changing the supply to the servos to being Vs, which is provided by an external source (Battery).
- Pin 7 needs to be set to high at the start of the program to ensure the version of the host shield works as intended.
- The power supply for 3 servo motors should be 6v and above 1amp (1.5/2amp). This is due to when they are all functional they draw a very large current causing other components in the system to recieve insufficient power.
- The USB Host shield requires around 7v 500mA to function properly, without this the USB port will not function.
- By removing the ``VL=VS`` header on the BotBoarduino the Logic and the Servos can be powered separately, which aids with the reliability of the Host shield. This is due to if the servos draw excessive current the USB device remains powered.

**Connections:**
``BOTBOARD ----> Host Shield``
- D7 ----> D7
- D10 ----> D10
- D11 ----> D11
- D12 ----> D12
- D13 ----> D13

- Currently the system is powered by the NI Virtual Bench Supply. +6v Terminal is connected to VS and +24v is set to 7.5v and connected to VL.

[Current Draw Test](https://github.com/lboroWMEME-19WSD001/B-Idea-Testing/blob/master/Servo%20Control/System%20current%20draw%20test%202019-10-24%2011-42-44.mp4)

- The speaker header has been removed as an intial move to supply more current to the servos.

**Sabertooth 2x12RC | Tracked Rover:**

This is documentation on how to use the Sabertooth 2x12RC

Header switches:
S1,S2,S4,S5,S6 --> DOWN
S3 --> UP
``001000``

- When writing to the motors use ``servo.writeMicroseconds(%num);`` where num is a value from 1000-2000
    - 1000 is both motors forwards, 2000 is both motors backwards and 1500 both stationary

**Sources:**
- https://github.com/felis/USB_Host_Shield_2.0/blob/master/XBOXRECV.h
- https://github.com/felis/USB_Host_Shield_2.0/blob/master/examples/Xbox/XBOXRECV/XBOXRECV.ino
- http://www.lynxmotion.com/images/html/build185.htm
- https://www.dimensionengineering.com/datasheets/Sabertooth2X12RCQuickStart.pdf

# Simulink | Optical Flow model

This is testing learnt knowledge on how to create a model to track movemnt within a video stream. All done in Matlab 2019b.

**Components and Libraries:**

- USB 1080p Camera
- MATLAB Support Package for USB Webcams (19.2.0)
- Symbolic Math Toolbox (8.4)
- Simulink Support Package for Raspberry Pi Hardware (19.2.0)
- Image Processing Toolbox (11.0)
- Computer Vision Toolbox (9.1)

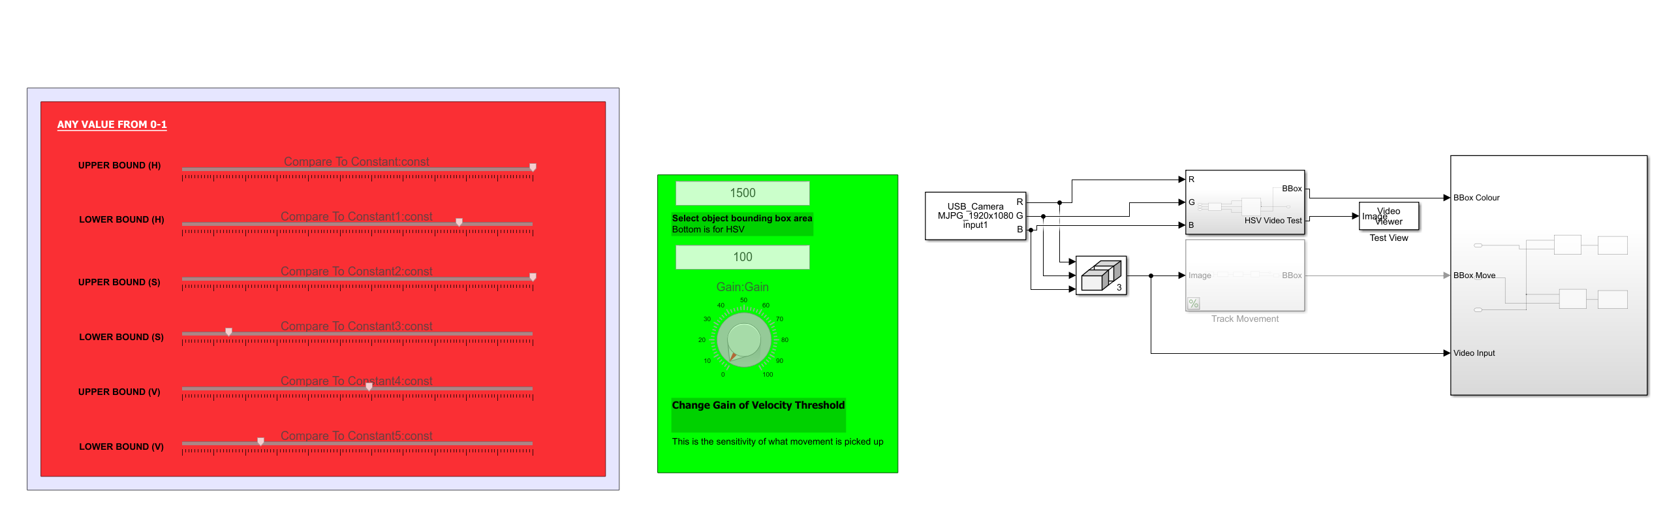
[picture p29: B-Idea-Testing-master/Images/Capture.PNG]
Top Level Model View


**Rundown:**

- Video stream input as RGB
- Converted to Intensity and fed into an Optical Flow Block
- The output: Intensity image showing the difference between the velocity of areas in the image
(Process could be sped up by changing the frames that are being compared. Currently every frame is compared to one another)
- This data is then filtered based on what velocities we care about (Thresholding)
- Bounding Box: Draws boxes around areas that we want to track. This block also outputs the central coords of each box in relation with the bottom left of the image (in pixels).

**Variables:**
- The minimum area tracked can be changed based on the size of the object being tracked (In pixels)
- The sensitivity can be changed by increasing the gain of the thresholding block

Both of these can be altered while the simulation is runnning.

[Video demonstration](https://www.youtube.com/watch?v=3YoWCa4jGAI)

# Rovertest

Tested the rovor motor to check weather they worked with some simple code on arduino the code simply accelerates both motors untill they reach 180 and then back down to zero. The test was conclusive and showed that both motors worked sucssesfully and can be coded. Other information used was found on the data sheet for the sabortooth 2x 12rc.

The code was simple and worked by checking that both motor were able to move in the forward and reverse direction.
This was done by creating a for loop that stated that when the motor was in position 0 it would move forward until the position was greater than 180, at which point it would leave the for loop and enter another for loop that would move the motor positions from 180 back down to 0.

**To note:**
- Switch 1 on the power board was set down so that each motor could be controlled independently and not in mixed mode.

**Source:**

- https://www.dimensionengineering.com/datasheets/Sabertooth2X12RCQuickStart.pdf

# Camera Tests

Four cameras were provided for the group, 2 HD 1080p cameras and 2 720p webcams. All of the cameras were tested using the same methodology:

1. Plug in power to camera/into a usb device

    +This was passed by all cameras
    
2. Using camera app on windows determine output recieved

    +All cameras displayed a video output when used in conjuction with the camera app
    
3. Visual inspection of the device
    if possible focus and unfocus lens to determine damage to lens

    +Of the cameras only the 1080p cameras had adjustable lenses 
    
    +The camera with the plain labeling was shown to be scratched on the lens
    
    +All of the cameras had scratches on the surface,
    however not impeding the performance in any noticable way
    
    +The 1080p camera with a red label was missing a base stand
    
    +The 720p webcam with a yellow label also had some pen markings on its surface
    
4. Record video using windows 10 camera app make sure to record movement and

5. View the propeties of the video and under the details section record resolution and frames per second rounding to nearest whole number

    +The webcams claiming to be 720p were so
    
    +The 1080p HD cameras were also the resolution given
    
    +The FPS tests revealed a variety of caputring speeds
    
        | Camera              | FPS |
        |--------------------:|:---:|
        | webcam plain        | 29  |
        | webcam yellow label | 27  |
        | 1080 cam plain      | 27  |
        | 1080 cam red label  | 21  |
        
     +These results indicate low resolution cameras to faster capturing speeds, 
     but may have been affected by the software used

# Inputs Tests
The input devices given to the group were, a usb mouse, a usb keyboard, a usb xbox 360 reciever and 2 xbox controllers.

1. All the devices usb devices were plugged into the usb socket of a computer running windows 10 to check if they were capable of recieving power (all devices have a led power indicator)
    + All of the usb devices passed this test successfully
2. The xbox controllers were tested for power by attempting to turn them on using the xbox home button
    + The controller labeled h did not turn on, however when the batteries were replaced it did
3. The mouse was then tested by moving it around and pressing all of the buttons to determine if any of those things were broken
    + They were not
4. The keyboard was then tested, a notepad document was opened and all of the number keys were pressed sequentially and all of the letter keys were then pressed in the order that are layed out on the board
    + All of those keys worked succesfully so it was assumed the keyboard was fully functional
5. The xbox controller and reciever were tested in conjunction, using the new connection button on both a controller and the reciever the devices were paired and the using the game controller diagnostics window located in Devices and Printers/(Controller)/Game Controller Settings/Properties and under the test tab. Then every button and axis was moved
    + The reciever was fully functional
    + The xbox controller labeled k was functional, however when returned to neutral positions the test 
    program registered them as not being in fully neutral position due to the analog sticks getting 
    slightly stuck
    + The xbox controller labeled h was fine
# Mbed Testing
The mbed was tested first by giving it mini usb power to check that it turned on then the mbed compiler's default blinky code was loaded
```C
while(1) {
        myled = 1;
        wait(0.2);
        myled = 0;
        wait(0.2);
    }
```
as this was not the code previously running on the device this meant that it passed the second test of being able to have code uploaded to it. This also verified that the leds on the main board worked
The application board of the mbed was then tested using programs on at https://os.mbed.com/cookbook/mbed-application-board using only programs prefixed with "app-board-". The RGB leds, Speaker, AnalogOut, Joystick and LCD were verified working using this procedure, the USB mouse input test code did not compile.
# Raspberry Pi Testing
The raspberry pi was tested firstly by pluging into a micro usb socket from a phone charger wall adapter and was determined able to recieve power when the leds on the board came on. An image was made of the current software on the raspberry pi's micro sd card and the latest version of raspbian for this board was downloaded onto the board following the instructions at https://www.raspberrypi.org/documentation/installation/installing-images/README.md . After this the raspberry pi was plugged into a monitor using an hdmi to vga adapter and the mouse and keyboard were also plugged in before giving the board power, this validated that the hdmi port and usb socket were functioning.
Then the pi logged in to and setup. Then using a python script the GPIOs
```Python
import RPi.GPIO as GPIO
GPIO.setup(GPIONUM,GPIO.OUT)
GPIO.output(GPIONUM,True)
```
accourding the this diagram https://www.element14.com/community/docs/DOC-73950/l/raspberry-pi-3-model-b-gpio-40-pin-block-pinout , it was assumed if a voltage could come out of a GPIO pin than it would be able to read a voltage as an input.

## Connecting raspberry pi to Matlab
Node graph

## Setting up multiple machines with ROS and raspberry pi
The .bashrc files of both machines were edited to identify the ROS machine as the master. A talker node was run on the ROS machine while a lister was run on the raspberry pi and it was show that data could be transmitted.
Node graph2
# Deep Learning

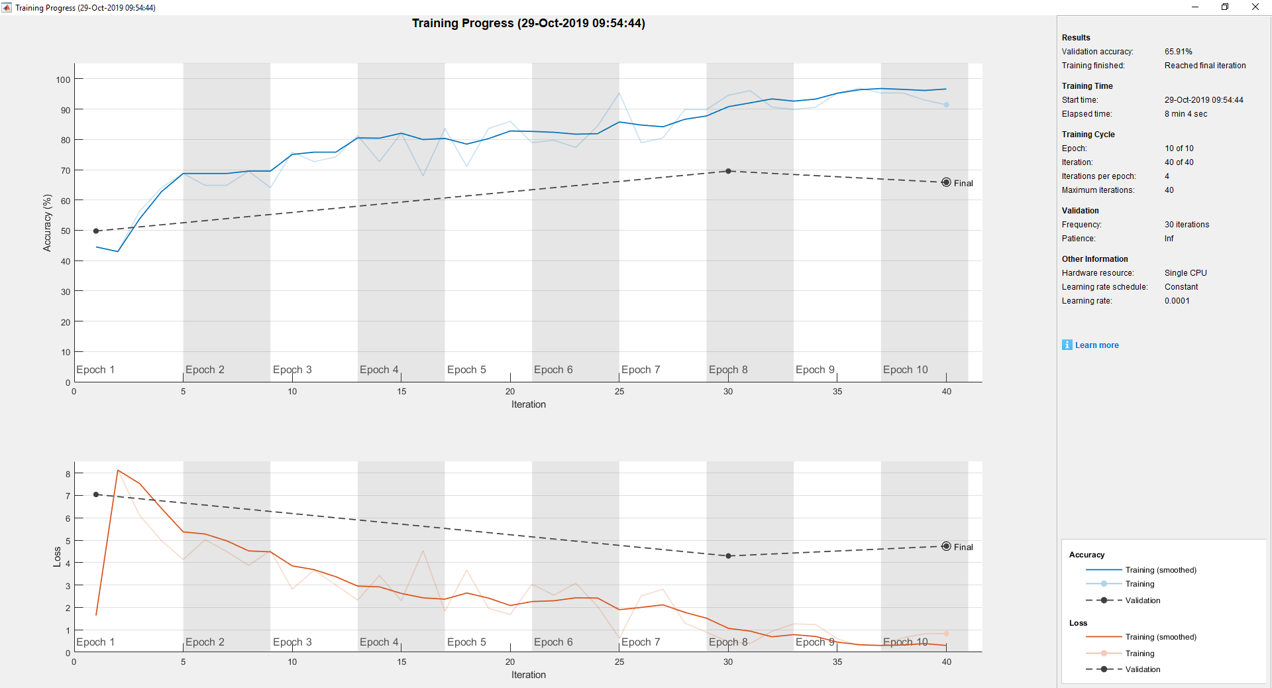
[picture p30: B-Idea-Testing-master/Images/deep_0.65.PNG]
Neural Net Training


# Blink LED using ROS 
The default blink LED code was tested to ensure the Arduino could upload code after the IDe was setup for linix, the code ran fine and upoloading was successful. Next was the supsciber example for ROS:
1. rosrun rosserial_python serial_node.py /dev/ttyACM0 was used to set up the connection 
1. rostopic list was used to get the list of topics
1. rostopic pub toggle_led std_msgs/Empty --once was supposed to blink the Arduino but no change occoured.
1. Subscriber needs to remain set up in its own terminal, trying the command again in new termial toggled the LED.
results image

# ROS Webpage Control with RosLibjs

This section followed a predocumented approach to the use of ROS Java Script libraries to create a usable control webpage to subscribe, publish and get usable data to view the running system. This system would also be able to view video outputs from all systems to better observe and remedy issues that may arise.

[Github Page:EESC-LabRoM](https://github.com/EESC-LabRoM/rosweb)

Following the tutorial on here this websocket server was installed on the Linux Ros machine.

Running the follwing will start the Ros Websocket Server locally:
``$ roslaunch rosbridge_server rosbridge_websocket.launch``

and to run the video server,

``$ rosrun web_video_server web_video_server``

HAS TO BE RUN IN A CHROME WINDOW : http://labrom.eesc.usp.br/rosweb/

# ROS Mono Slam with OrbSlam2

This section details how ORB Slam V2 was implemented using opensource ros packages to simultaneously localise our robot and map an environment to avoid collisions. This is a monocular system since we are intending on implementing this with one usb webcam due to the raspberry pi3 being more reliable when using one camera. To be able to use stereo vision we would have to upgrade to a RPI 4 or use two RPI 3's.

This has been implemented using: (ORB SLAM V2)[https://github.com/appliedAI-Initiative/orb_slam_2_ros]

**Alterations have been made to the following files in the following folders! These will need changing if either the camera changes or if the environement changes (Current Environment: PROJECT ROOM)**

- ``/home/catkin_ws/src/orb_slam_2_ros/orb_slam2/config/head_camera.yaml``

This file determines the camera parameters after being normalised to remove abberation from the fish eye effect.
This can be done through ``$ rosrun camera_calibration cameracalibrator.py --size 6x4 --square 0.114 image:=/usb_cam/image_raw camera:=/usb_cam``. Changing the parameters where necessary.

- ``/home/catkin_ws/src/orb_slam_2_ros/ros/launch/orb_slam2_headcamera_mono.launch``

This file contains the necessary information for running the launching of ORBSLAM2. This can be changed to accomodate for 
a different camera publisher by changing the 'to.' inside the remap to that of the camera publisher being used.
In this case it is usb_cam/image_raw

**RUNNING THE PROGRAM (STEP-BY-STEP)**

*ensure that in every terminal catkin_ws is sourced!*

1. ``$ roscore``
2. ``$ roslaunch usb_cam usb_cam-test.launch``
3. ``$ roslaunch orb_slam2_ros orb_slam2_headcamera_mono.launch ``
4. ``$ rviz``

Use ``$ rqt_graph`` to double check if all the nodes and topics are correct!

*Example:*
RQT Graph for OrbSlamV2

**Using RVIZ to visualise a crude URDF Model of the Tri-Track**
Tri-Track URDF Model

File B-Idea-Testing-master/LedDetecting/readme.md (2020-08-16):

# LED detecting code

inital light detecting code found at

https://www.pyimagesearch.com/2016/10/31/detecting-multiple-bright-spots-in-an-image-with-python-and-opencv/
http://t.dripemail2.com/c/eyJhY2NvdW50X2lkIjoiNDc2ODQyOSIsImRlbGl2ZXJ5X2lkIjoiODY2NzI2MDMyOCIsInVybCI6Imh0dHA6Ly9weWltZy5jby81cmRtaz9fX3M9cWV0eTIxY3NxZjFpNTd6emlyeXM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

After detecting lights it will cycle through the lights and take point around the light(labeled in green in the output image) and test for their color if the color is within a band on an hsv curve for hue (currently set to max band) it will be determined to be red, green or blue this will then be compared for each point to reach a consensus on color and add that to a list of numbered lights from left to right and their color.
The next step is to apply this to video and then determine flashing patterns

# How to run

1. install opencv, numpy and skimage for python 3
2. edit line 48 ( currently reading image = cv2.imread("/home/leo/Downloads/multiple-bright-spots/images/lights_02.png") ) to point to input image path
3. run in python 3
4. an image will be output in the directory you run the file in or in the directory the file is stored if using idle

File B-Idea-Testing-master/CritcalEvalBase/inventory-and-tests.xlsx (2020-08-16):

what do we have
 | robotics | inputs | circuit stuff | micro controlllers | power | cameras | miss | cables
 |  | mouse | breadboard
 | mars rover ( tracked bot) | 2 xbox controllers |  | arduino bot b 2 | 3700 battery band x2 | 2 web cams | 2 tool boxes | ethernet
 | robotics arms x2 | keyboard |  | ras pi 3.0 | rechargable battery charger | 2 1080p cams | wooden board | micro usb x3
 | ultra tribike (3 wheel bot) | xbox recivers |  | mbed | 3000 mAH battery x2 |  |  | tybe b usb
 |  |  |  | arduino uno |  |  |  | battery pack chargers x2
 |  |  |  | my rio x2 |  |  |  | 2x micro HDMI
robotics |  | Turns on | Motors move | condition |  |  |  | usb type A
 | mars rover ( tracked bot) | y | y |  |  |  |  | battery charger kit for rechagable batterys
 | robotic arm | y | y |  |  |  |  | 1x VGA cable
 | ultra tribike (3 wheel bot) | y | y | power issues and possible damage motors |  |  |  | 1x VGAB cable
 | robotic arm (handless) |  |  | missing hand
Microcontroller tests | Name | Turns on | Can be programmed | Do peripherals work | Any signs of damage
 | arduino bot b 2 | Y | Y | Some motor control problems | N
 | ras pi 3.0 | Y | Y | y | N
 | mbed | Y | Y | y ( RGB leds, Speaker,AnalogOut,Joystick, LCD, and on board LEDs work, USB mouse input test code did not compile) | N
 | arduino uno | y | y | y | n
 | my rio I | y | y | y | n
 | my rio D | y | y | y | n
 |  |  | z
Power tests |  | Turns on
 | 3700 battery band x2 | y
 | rechargable battery charger | y
 | 3000 mAH battery x2 | y
input tests |  | recieves power | button/axis work | physical condition
 | mouse | y | y | good
 | xbox controller k | y | y | left and right joystick stable off center
 | xbox controller h | y | y | good
 | keyboard | y | y | good
 | xbox reciever | y | y | good
Cameras |  | recieves power | outputs video | physical condition | resolution | fps (will be subject to software and hardware involved)
 | webcam plain | y | y | scratched but camera is fine | 1280x720 | 29
 | webcam yellow | y | y | scratched and marked with pen camera is fine | 1280x720 | 27
 | 1080 cam plain | y | y | scratched on lens and all over | 1920x1080 | 27
 | 1080 cam red 1 | y | y | missing a base lens is dirty | 1920x1080 | 21

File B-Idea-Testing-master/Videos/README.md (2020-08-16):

**This folder contains videos to prove tests having been done!**

**Other videos can be found on team members youtube channels, such as [Dan Blenkarn](https://www.youtube.com/channel/UCvwY6f526kItW6sCyGKP6Vg).**

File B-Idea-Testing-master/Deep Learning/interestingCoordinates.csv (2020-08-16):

centroidsX | centroidsY
18 | 42
52.5 | 891
87 | 34
213.514285714286 | 870.028571428571
214 | 877
218.263157894737 | 856.157894736842
217.636363636364 | 862.272727272727
219.415094339623 | 879.962264150943
222 | 867.25
222 | 842
223 | 871.5
228.045454545455 | 864.863636363636
236.620689655172 | 878.48275862069
232 | 885.5
237.375 | 854.8125
239.857142857143 | 873.285714285714
242.384615384615 | 869
243.25 | 875
423.194075752671 | 212.214848386749
338 | 856
427 | 874
434.195652173913 | 768.326086956522
443.052631578947 | 217.473684210526
466.083333333333 | 195.333333333333
479.75 | 292
485.5 | 258
506.275 | 249.975
529.006430868167 | 304.871382636656
525.504032258065 | 133.157258064516
520.272727272727 | 156.636363636364
530.207547169811 | 265.735849056604
527.5 | 323
552.707070707071 | 158.737373737374
539.926553672316 | 145.389830508475
542 | 271.5
549.4 | 274.133333333333
547.333333333333 | 184.888888888889
548.5 | 825
548 | 876
549 | 143.5
550 | 718
558.5 | 277
571.037037037037 | 297.296296296296
565.638888888889 | 272.055555555556
566.666666666667 | 285.333333333333
572.772727272727 | 345.295454545455
571.387096774194 | 172.451612903226
575.691489361702 | 242.815602836879
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

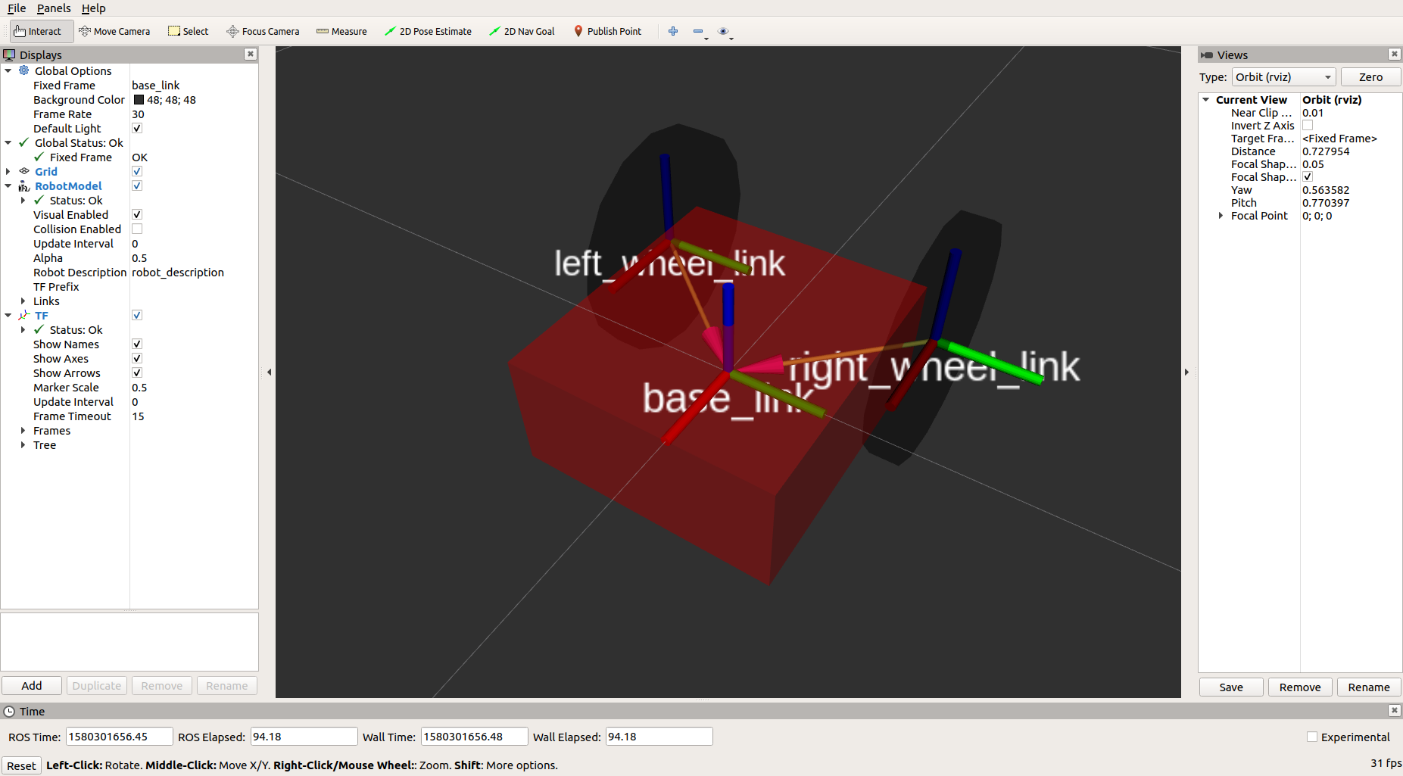
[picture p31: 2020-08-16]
B-Idea-Testing-master/Images/rviz_tri_track.png

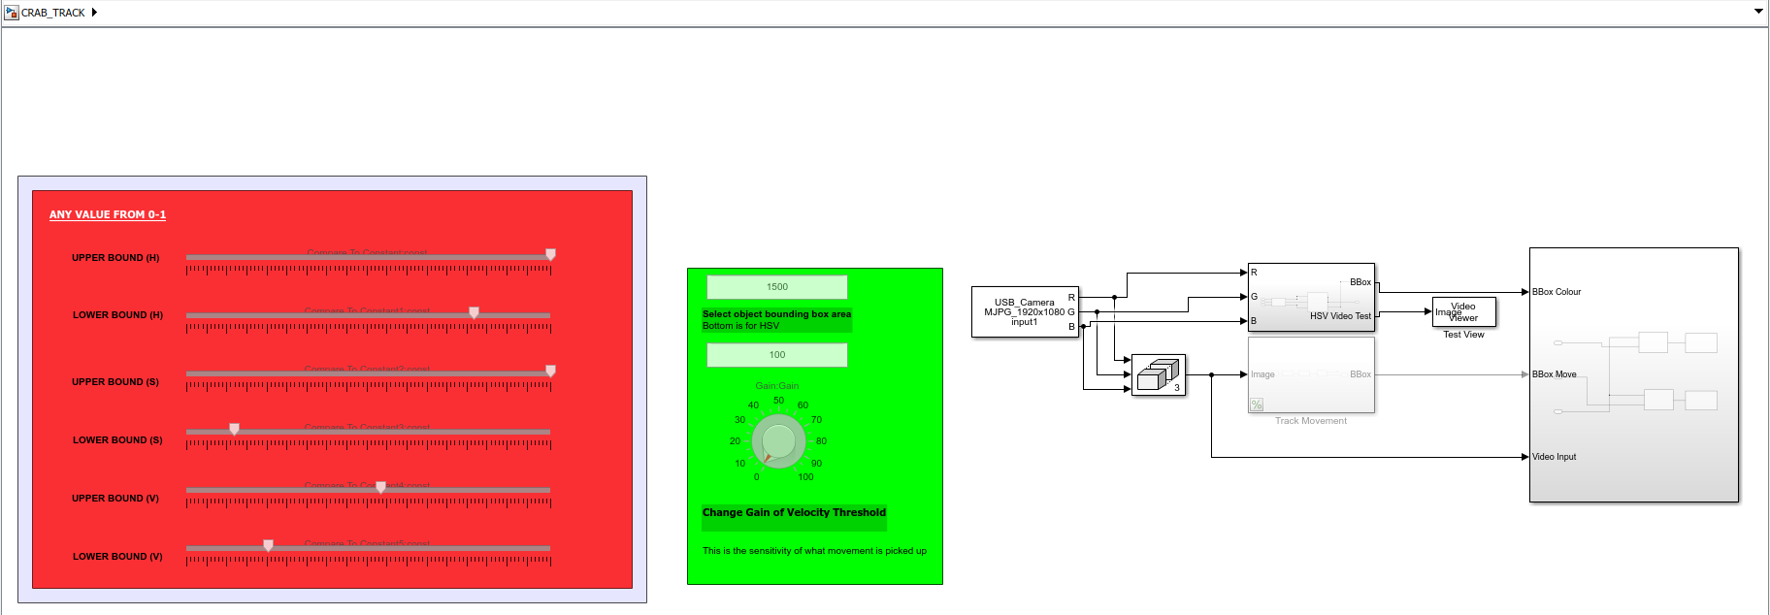
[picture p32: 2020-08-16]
B-Idea-Testing-master/Images/crabtrack.PNG

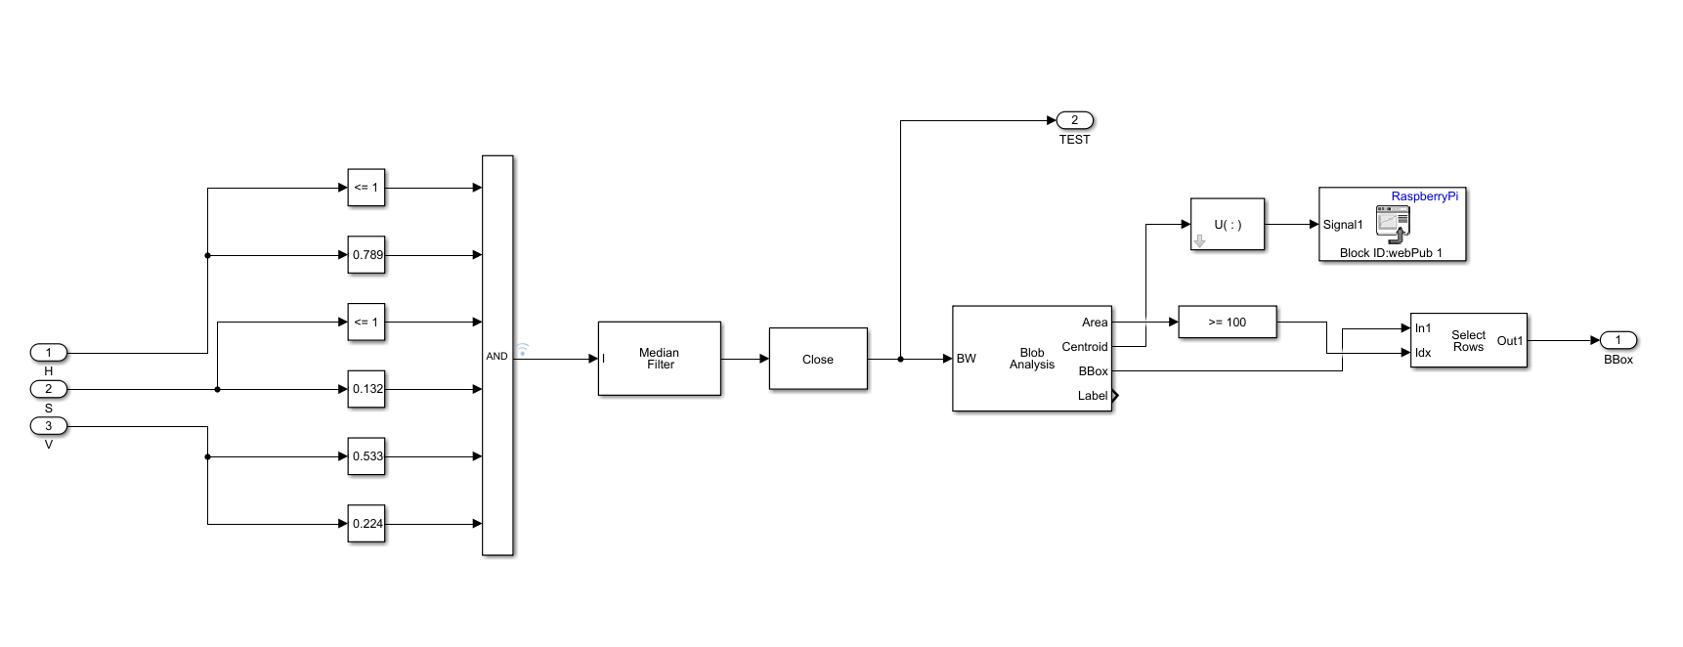
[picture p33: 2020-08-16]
B-Idea-Testing-master/Images/crabtrack_compare.PNG

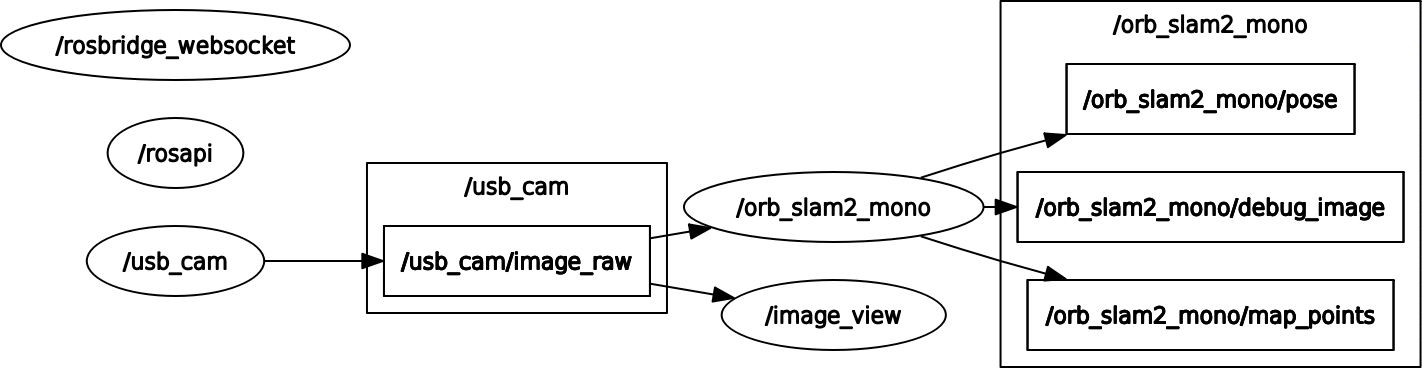
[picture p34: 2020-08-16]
B-Idea-Testing-master/Images/rosorbslam2.png

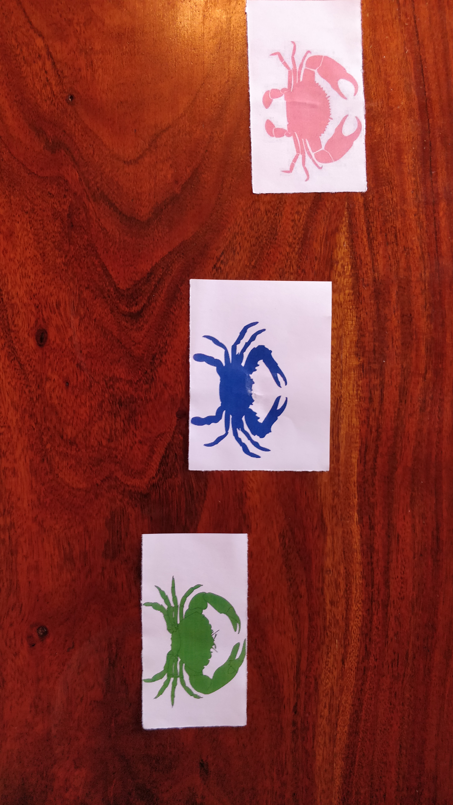
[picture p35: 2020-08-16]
B-Idea-Testing-master/Simulink Tests/crab3.jpg

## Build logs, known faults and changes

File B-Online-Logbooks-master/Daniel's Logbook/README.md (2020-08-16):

# DANS LOGBOOK

This will include anything that is too long or can only be accessed online.

# 21/10/2019 | Simulink Machine Vision

- [Optical Flow, Moving Object Tracking](https://youtu.be/3YoWCa4jGAI)

This is a short video depicting an initial test performed to assess the capabilities of simulink for machine vision. This                 is using an Optical Flow method which determines the change between two frames and masks the area which has changed.                       The program currently checks every frame to the last which could be slow/inefficient when used on a raspberry pi, but that                 can be adapted. There is also a variable value which determines the minimum size of each bounding box to be displayed,                     this prevents every possible change being displayed. This also uses blob analysis to determine where to draw the boxes based off the intensity image, which depicts what areas have moved.

# 24/10/2019 | Tracked Robot and Arm Testing

- [Robot Testing Compilation](https://www.youtube.com/watch?v=stPPC0m9og8)

This video depicts the outcomes of some tests that were performed to create an easy to use program that could be integrated with a wireless device in the future. This would allow the robot to connect to ROS quickly and easily allowing for better integration in the future.
In this video the robot is shown to be able to be controlled fully along with a 3 servo motor robotic arm, all using the same control board (Botboarduino), USB Host Shield and an Xbox controller. 

**Limitations:**

The whole system was powered through a National Instruments VirtualBench, supplying ``6V 1A and 7.5V 0.5A``. This was done due to the number of servo motors being used was drawing far too much current, causing the USB Host shield to not function correctly. The other downside of this setup is that only 4 motors can run concurrently. The solution to this is to use the SSC-32 Servo Motor control board, which will allow all of the motors to be powered on a separate board, thus increasing the reliability of the system. The robot also requires a system to transform the input from a 12V battery to roughly the same inputs as used from the Virtual Bench.

**Links To Components To Test**

- https://www.amazon.co.uk/Valefod-Efficiency-Voltage-Regulator-Converter-8-Pack/dp/B07DYP6L35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

*This is a buck converter to allow the use of the 12V battery with the botboarduino*

- [ ] Owned

-https://www.sparkfun.com/products/13678

*This is a wireless adapter. Connects via SPI and has built in TCP/IP protocols which allows it to work with the arduino platform*

- [ ] Owned

https://www.selectsolar.co.uk/prod/269/powerfilm-pt72150-200ma-72v-mini-solar-panel

*Flexible/Durable small solar panel for use atop a robot to increase its activity time whilst cleaning a beach*

- [ ] Owned

# 07/03/2020 | RTAB MAP Stereo Mapping+Navigation

Replacing orb-slam with Stereo slam using RTab map.

- https://github.com/introlab/rtabmap/wiki/Stereo-mapping

- http://wiki.ros.org/rtabmap_ros/Tutorials/SetupOnYourRobot#Stereo_A

- http://wiki.ros.org/viso2_ros

- http://wiki.ros.org/vision_opencv

# 09/03/2020 | RTAB MAP Stereo Mapping+Navigation: PART 2

- https://answers.ros.org/question/274701/rtabmapstereo-cameratwo-web-cam/

- https://answers.ros.org/question/267915/rtabmap-non-overlapping-3d-cloud/

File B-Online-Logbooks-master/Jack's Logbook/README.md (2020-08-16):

### Useful websites 

###  **06/01/2020**

Rack and pinion gear for fork lift design (lego):http://www.technicopedia.com/850/850cfork.JPG

video of rack and pinion working:https://www.youtube.com/watch?v=3_Bq3Zj3838
###  **10/12/2019**

Cad design drawing for motor to syringe: https://grabcad.com/library/rack-pinion-assembly-2

### **13/11/2019**
suitable motor for the rack and piston gear: https://uk.rs-online.com/web/p/dc-geared-motors/8347647/

Data sheet for the motor we already have: https://www.servocity.com/hs-645mg-servo

Similar robotic arm to what i want: https://www.youtube.com/watch?v=XrgeOfFyGLI

### **11/11/2019**
ID robot chemical tagging for rubbish:  https://www.sciencedirect.com/topics/chemistry/chemical-sensor

Building a prototype robtic arm using syringes:  https://www.youtube.com/watch?v=P2r9U4wkjcc

Controlling arm using arduino and hydralics:  https://www.youtube.com/channel/UCR28COcUV14J4OPGiPXPiZQ  

Designing a worm gear on CAD:  https://www.youtube.com/watch?v=zjSCypsKnTE

### **04/11/2019**
Tide table:  https://en.wikipedia.org/wiki/Tide_table

Tide predicting machine:  https://en.wikipedia.org/wiki/Tide-predicting_machine

How stuff works:  https://science.howstuffworks.com/environmental/earth/oceanography/tide-table1.htm

detecting colour:  https://fortop.co.uk/solutions/products/colour-sensors/

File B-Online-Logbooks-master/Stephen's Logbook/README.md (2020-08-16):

# Logbook
### Contains links used to complete various tasks in the project.

## **15/03/20**
Become super user: https://askubuntu.com/questions/617850/changing-from-user-to-superuser

## **10/03/20**
Pi 3 and ubuntu: https://www.raspberrypi.org/forums/viewtopic.php?f=56&t=220079

## **10/03/20**
Subscriber: https://github.com/engcang/HC-SR04-UltraSonicSensor-ROS-RaspberryPi/blob/master/ROS_sonar_sensor.py

## **09/03/20**
**Raspberry Pi ultrasonic:**
1. https://thepihut.com/blogs/raspberry-pi-tutorials/hc-sr04-ultrasonic-range-sensor-on-the-raspberry-pi
1. https://tutorials-raspberrypi.com/raspberry-pi-ultrasonic-sensor-hc-sr04/

Raspberry Pi accel: http://blog.bitify.co.uk/2013/11/reading-data-from-mpu-6050-on-raspberry.html

## **08/03/20**
**Raspberry Pi waterproof:** 
1. https://sixfab.com/product/raspberry-pi-ip65-weatherproof-iot-project-enclosure/
1. https://www.raspberrypi.org/blog/waterproof-3d-printing-raspberry-pi/
1. https://www.instructables.com/id/RainBerry-Compact-Weatherproof-Case-for-Raspberry-/
1. https://www.tomshardware.com/news/waterproof-your-raspberry-pi,40446.html

## **05/02/20**
Working pi SPI code: https://core-electronics.com.au/tutorials/i-spi-with-raspberry-pi.html

Working arduino SPI code: https://forum.arduino.cc/index.php?topic=184527.0
## **03/02/20**
Sending strings with pyserial: https://stackoverflow.com/questions/22275079/pyserial-write-wont-take-my-string

## **02/02/20**
Read Arduino serial data: https://www.youtube.com/watch?v=VIa_QZWIonQ

## **01/02/20**
Installing Arduino IDE: https://www.arduino.cc/en/guide/linux#toc2 

## **31/01/20**
### Logic level conversion:
  1. https://core-electronics.com.au/tutorials/logic-level-converters-for-raspberry-pi.html
  1. https://media.digikey.com/pdf/Data%20Sheets/Sparkfun%20PDFs/Bi-Directional-Logic-Level_HookupGuide.pdf
  
### SPI communication:
  1. http://mitchtech.net/raspberry-pi-arduino-spi/

## **30/01/20**
### Pi and Arduino USB serial communication: 
  1. https://www.instructables.com/id/Raspberry-Pi-Arduino-Serial-Communication/
  1. http://www.penguintutor.com/electronics/rpi-arduino
  1. https://tutorials-raspberrypi.com/how-to-arduino-raspberry-pi-communication/

## **29/01/20**
Blinking LED raspi: https://roboticadiy.com/how-to-blink-led-with-raspberry-pi-4/

Flash an arduino with Raspberry Pi: https://www.youtube.com/watch?v=QumIhvYtRKQ

Raspi and Arduino serial connection: https://www.youtube.com/watch?v=KmjLOhDrqWg

## **28/01/20**

Raspberry Pi to Arduino SPI Communication: http://robotics.hobbizine.com/raspiduino.html

pip python spidev: https://pypi.org/project/spidev/

Installed pip: sudo apt install python-pip

## **27/01/20** 

Launch ROS node over wifi: https://answers.ros.org/question/232774/launch-a-ros-node-over-wifi/

ROS serial for ESP8266 through WiFi: https://github.com/agnunez/espros

Using UDP transport data to Non-ROS computer over UDP
: https://stackoverflow.com/questions/34564842/using-udp-transport-data-to-non-ros-computer-over-udp

Raspberry Pi (master) Arduino Uno (slave) SPI communication with WiringPi: https://roboticsbackend.com/raspberry-pi-master-arduino-uno-slave-spi-communication-with-wiringpi/

How to define GPIO pins in ROS on a Raspberry Pi: https://answers.ros.org/question/232819/how-to-define-gpio-pins-in-ros-on-a-raspberry-pi-2/

HOW TO WRITE C PROGRAM IN UBUNTU: https://www.improgrammer.net/how-to-write-c-program-in-ubuntu/

## **24/01/20**

Cloning a raspi SD card: https://www.howtogeek.com/341944/how-to-clone-your-raspberry-pi-sd-card-for-foolproof-backup/

## **22/12/19**

 * **None of the previous tutorials work with the pi4 ROS build** 

## **21/12/19**

  * Flashed B2 pi
  * Setup SSH for B2 pi
  * Setup B2 as slave to B1
  
Camera publisher for Pi: https://answers.ros.org/question/192885/how-to-publisher-image-and-camera/

## **20/12/19**

Using usb camera on Raspberry Pi: https://www.raspberrypi.org/documentation/usage/webcams/ 

## **19/12/19**

Matlab won't build code making it impossible to use to create nodes. Consider manual bulilding.

## **18/12/19**

Getting Started with Robot Operating System (ROS) on Raspberry Pi: https://uk.mathworks.com/help/supportpkg/raspberrypi/examples/getting-started-with-robot-operating-system-ros-on-raspberry-pi-r.html

## **17/12/19**

Setting up wpa_supplicant on Rasperry Pi: https://www.raspberrypi-spy.co.uk/2017/04/manually-setting-up-pi-wifi-using-wpa_supplicant-conf/

## **16/12/19**

Raspberry Pi image for flashing: https://www.raspberrypi.org/downloads/raspbian/

Installing operating system images: https://www.raspberrypi.org/documentation/installation/installing-images/README.md

SD card memory formatter for windows: https://www.sdcard.org/downloads/formatter/eula_windows

Raspberry Pi image with ROS : https://roboteurs.com/pages/raspberry-pi-4-ros-opencv-image

setting up wifi with wpa_supplicant: https://www.youtube.com/watch?v=xu7exZ1WJHw
## **15/12/19**

Setting up ROS on raspi: https://www.instructables.com/id/ROS-Melodic-on-Raspberry-Pi-4-RPLIDAR/

overscan on raspi (didn't work): https://www.opentechguides.com/how-to/article/raspberry-pi/28/raspi-display-setting.html
## **14/11/19**

How to set up a virtual machine: https://www.groovypost.com/howto/howto/setup-virtualbox-windows-7/

Not enough storage to set one up.

## **06/12/19**

Raspberry Pi and camera node with matlab: https://uk.mathworks.com/help/supportpkg/raspberrypi/examples/stream-images-from-raspberry-pi-using-robot-operating-system-ros.html

How to connect raspberry pi to ROS network using Matlab: https://uk.mathworks.com/help/ros/ref/rosdevice.html

Getting Started with Robot Operating System (ROS) on Raspberry Pi: https://uk.mathworks.com/help/supportpkg/raspberrypi/examples/getting-started-with-robot-operating-system-ros-on-raspberry-pi-r.html

Getting started with simulink: https://uk.mathworks.com/help/ros/ug/get-started-with-ros-in-simulink.html

## **03/12/19**

Completed tutorial to set up ROS on multiple machines and tested the connection with talker and listener nodes.

## **02/12/19**

ROS multiple network setup: https://wiki.ros.org/ROS/NetworkSetup

How to use netcat: https://linoxide.com/linux-how-to/install-use-netcat-command-linux/

How to set up ROS master on multiple machines: https://www.youtube.com/watch?v=1KOrXSEDQ3k 

## **01/12/19**

Completed publisher and subscriber tutorial with Matlab: https://uk.mathworks.com/help/ros/ug/exchange-data-with-ros-publishers-and-subscribers.html 

Communication between Raspberry Pi and PC (ROS) setup: https://github.com/mktk1117/six_wheel_robot/wiki/Communication-between-Raspberry-Pi-and-PC-(ROS)

## **29/11/19**

Getting Started with MATLAB Support Package for Raspberry Pi: https://uk.mathworks.com/videos/install-the-matlab-support-package-for-raspberry-pi-94266.html

Connect to a ROS network: https://uk.mathworks.com/help/ros/ug/connect-to-a-ros-network.html

## **27/11/19**

Setting up ROS on Raspberry Pi: https://wiki.ros.org/ROSberryPi/Installing%20ROS%20Indigo%20on%20Raspberry%20Pi

ROS and Matlab: https://uk.mathworks.com/help/ros/getting-started-with-ros-toolbox.html

### **24/11/19**
---
Fixed Arduino not uploading code:  uninstalled and ran Arduino set up script.

Completed the blink LED tutorial using ROS, it contained and extra step involving a sensor (MPU-9150) we could use to get data : https://www.servomagazine.com/magazine/article/November2016_ROS-Arduino-Interfacing-for-Robotics-Projects 

## **21/11/19**

New tutorial for rosserial: https://www.youtube.com/channel/UCIpjehUq_j7OMnTl8MvSJrw/playlists

Tutorial for rosserial arduino:http://wiki.ros.org/rosserial_arduino/Tutorials/Arduino%20IDE%20Setup

Rosserial overview: http://wiki.ros.org/rosserial/Overview

Finished install of rosserial + Arduino IDE set up.

## **20/11/19**

Error installing rosserial, missing rosserial_arduino.

## **19/11/19**

Setting up Ros on arduino: https://www.servomagazine.com/magazine/article/November2016_ROS-Arduino-Interfacing-for-Robotics-Projects

ROS on RasPi: https://roboticsbackend.com/install-ros-on-raspberry-pi-3/

RasPi, ROS and Simulink: https://uk.mathworks.com/help/supportpkg/raspberrypi/examples/getting-started-with-robot-operating-system-ros-on-raspberry-pi-r.html

## **16/11/19**

created bash script to source environment.

## **15/11/19 **

Debugged and got talker and listener executables working.

## **14/11/19**

Installed emacs and created talker.cpp file to prrepare for ROS subscriber tutorial.

Error using catkin_make, need to debug.

## **13/11/19**

Completed services tutorial: https://wiki.ros.org/ROS/Tutorials/UnderstandingServicesParams

Completed rqt_console and ros_launch tutorial: https://wiki.ros.org/ROS/Tutorials/UsingRqtconsoleRoslaunch

Completed Using rosed to edit files in ROS Tutorial: https://wiki.ros.org/ROS/Tutorials/UsingRosEd

Stated publisher/subscriber tutorial: https://wiki.ros.org/ROS/Tutorials/WritingPublisherSubscriber%28c%2B%2B%29
## **10/11/19**

Finished topics and nodes: https://wiki.ros.org/ROS/Tutorials/UnderstandingTopics

## **08/11/19**

Fixed software update issue and installed net tools: https://www.nixcraft.com/t/unable-to-locate-package-on-ubuntu-linux-when-using-apt-get/1077/4 

Aquired IP address of linux machine: 158.125.52.89 

## **07/11/19**

How to remote control a linux server using VNC: https://www.makeuseof.com/tag/remote-control-linux-windows/

Remote control with secure shell (SHH) : https://www.digitalocean.com/community/tutorials/how-to-use-ssh-to-connect-to-a-remote-server-in-ubuntu

## **04/11/19**

Completed ROS packages moving on to nodes: http://wiki.ros.org/ROS/Tutorials/UnderstandingNodes

Completed ROS node and ran turtle sim and renamed it to my_turtle.

Started ROS topics: http://wiki.ros.org/ROS/Tutorials/UnderstandingTopics error installing rtq_graph, need to look into it.

## **31/10/19**

Linux file commmands: https://www.dyclassroom.com/reference-linux/linux-commands-working-with-files-and-directories  

Finished set up of the ROS environment setup: https://wiki.ros.org/ROS/Tutorials/InstallingandConfiguringROSEnvironment

Navigating ROS file system: https://wiki.ros.org/ROS/Tutorials/NavigatingTheFilesystem 

Started package.xml setup: http://wiki.ros.org/ROS/Tutorials/CreatingPackage 

## **29/10/19**

ROS and arduino: http://lsi.vc.ehu.es/pablogn/investig/ROS/ROS-arduino.pdf

ROS arduino setup tutorial: https://www.servomagazine.com/magazine/article/November2016_ROS-Arduino-Interfacing-for-Robotics-Projects

ROS for beginners tutorial: https://wiki.ros.org/ROS/Tutorials

## **27/10/19**

How Do Electrostatic Air Filters Work?: https://www.hunker.com/12167146/how-do-electrostatic-air-filters-work 

River cleaning: https://youtu.be/RkQbcrzyAeE

4 Oceans river skimmer: https://youtu.be/stZcW-b8lT0

The ocean clean up: https://youtu.be/O1EAeNdTFHU

## **26/10/19**

Step by step guide to make a hello world program in labview: https://youtu.be/uRWhGq7UN74

How to seperate micro plastics from sand: https://youtu.be/O2LtQkGARAg

How to build a RC submarine: https://www.liveabout.com/what-do-you-need-to-build-an-rc-submarine-2863059

How to build an underwater robot: https://www.instructables.com/id/Build-an-Underwater-robot/

Gravity separation of polymers: https://m.youtube.com/watch?feature=youtu.be&v=0O2ehDqzBY0

## **13/10/19**

How the Kinect Depth Sensor Works in 2 Minutes: https://www.youtube.com/watch?v=uq9SEJxZiUg 

Kinect Recording Data Tutorial: https://www.youtube.com/watch?v=0RUpY0S0f4o 

DIY Kinect Motion Capture Studio | Blender: https://www.youtube.com/watch?v=1UPZtS5LVvw

## **11/10/19**

Intro to DIY Raman Spectroscopy: https://www.youtube.com/watch?v=tRrOdKW06sk

Removing microplastics is this easy!: https://www.youtube.com/watch?v=HcrSYbNqYdo&t=329s

How to Identify Any Type of Plastic | Orange Plastics Academy: https://www.youtube.com/watch?v=K3TL5k243YU

How to build your own: CD Spectroscope - Science Snacks activity: https://www.youtube.com/watch?v=1iWdTbXvHx0&t=72s 

Building a Nanodrop Style UV/Vis Spectrometer: https://www.youtube.com/watch?v=pIk8I10ZmYY&t=708s 

The Big Sort: An Insider's Tour of a Recycling Plant: https://www.youtube.com/watch?v=nUrBBBs7yzQ 

Identification and Analysis of Plastics in Recycling by NIR Hyperspectral camera KUSTA1.9MSI: https://www.youtube.com/watch?v=eIZIWSj7jIg&t=13s

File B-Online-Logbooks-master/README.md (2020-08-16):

# Logbooks

Supporting evidence for logbooks will be presented here.

The format should be as follows:

### **Date in bold heading 3** **DD/MM/YYYY**
A short description/title for the link. 

## How to use markdown
.md files use a special syntax for formatting, [click here](https://guides.github.com/features/mastering-markdown/) for the syntax, and [click here](https://help.github.com/en/categories/writing-on-github) for more syntax.

There is also a preview changes button - it does what it says.

If anything is unclear **just ask.**

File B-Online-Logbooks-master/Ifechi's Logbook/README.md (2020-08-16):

### 21/10/2019 | Picture Upload

Research in the zip file including research into ROS and drones, block diagram of the project and other research.

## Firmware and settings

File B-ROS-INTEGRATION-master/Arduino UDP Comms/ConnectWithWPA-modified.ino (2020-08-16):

/*

 This example connects to an unencrypted WiFi network.
 Then it prints the  MAC address of the WiFi shield,
 the IP address obtained, and other network details.

 Circuit:
 * WiFi shield attached

 created 13 July 2010
 by dlf (Metodo2 srl)
 modified 31 May 2012
 by Tom Igoe
 */
#include <SPI.h>
#include <WiFi101.h>
#includ <WiFiUdp.h>

#include "arduino_secrets.h" 
///////please enter your sensitive data in the Secret tab/arduino_secrets.h
char ssid[] = SECRET_SSID;        // your network SSID (name)
char pass[] = SECRET_PASS;    // your network password (use for WPA, or use as key for WEP)
int status = WL_IDLE_STATUS;     // the WiFi radio's status

unsigned int localPort = 2390;

WiFiUDP Udp;

void setup() {
  WiFi.setPins(8,7,4);
  //Initialize serial and wait for port to open:
  Serial.begin(9600);
  while (!Serial) {
    ; // wait for serial port to connect. Needed for native USB port only
  }

  // check for the presence of the shield:
  if (WiFi.status() == WL_NO_SHIELD) {
    Serial.println("WiFi shield not present");
    // don't continue:
    while (true);
  }

  // attempt to connect to WiFi network:
  while ( status != WL_CONNECTED) {
    Serial.print("Attempting to connect to WPA SSID: ");
    Serial.println(ssid);
    // Connect to WPA/WPA2 network:
    status = WiFi.begin(ssid, pass);
    // wait 10 seconds for connection:
    delay(10000);
  }
  Udp.begin(localPort);
  // you're connected now, so print out the data:
  //Serial.print("You're connected to the network");
  //printCurrentNet();
  //printWiFiData();
  
}

void loop() {
  // check the network connection once every 10 seconds:
  //delay(10000);
  //printCurrentNet();
  int packetSize = Udp.parsePacket();
  if (packetSize)
  {
    //Serial.print("Received packet of size ");
    //Serial.println(packetSize);
    //Serial.print("From ");
    IPAddress remoteIp = Udp.remoteIP(192.168.0.100);
    //Serial.print(remoteIp);
    //Serial.print(", port ");
    //Serial.println(Udp.remotePort());

    // read the packet into packetBufffer
    int len = Udp.read(packetBuffer, 362); //the number 361 is to be mapped to stop
    if (len > 0) packetBuffer[len] = 0;
    //Serial.println("Contents:");
    //Serial.println(packetBuffer);
    
    // send a reply, to the IP address and port that sent us the packet we received
    //Udp.beginPacket(Udp.remoteIP(), Udp.remotePort());
    //Udp.write(ReplyBuffer);
    //Udp.endPacket();
  }


  
}

//void printWiFiData() {
  // print your WiFi shield's IP address:
  //IPAddress ip = WiFi.localIP();
  //Serial.print("IP Address: ");
  //Serial.println(ip);
  //Serial.println(ip);

  // print your MAC address:
  //byte mac[6];
  //WiFi.macAddress(mac);
  //Serial.print("MAC address: ");
  //printMacAddress(mac);

//}

//void printCurrentNet() {
  // print the SSID of the network you're attached to:
  //Serial.print("SSID: ");
  //Serial.println(WiFi.SSID());

  // print the MAC address of the router you're attached to:
  //byte bssid[6];
  //WiFi.BSSID(bssid);
  //Serial.print("BSSID: ");
  //printMacAddress(bssid);

  // print the received signal strength:
  //long rssi = WiFi.RSSI();
  //Serial.print("signal strength (RSSI):");
  //Serial.println(rssi);

  // print the encryption type:
  //byte encryption = WiFi.encryptionType();
  //Serial.print("Encryption Type:");
  //Serial.println(encryption, HEX);
  //Serial.println();
/}

//void printMacAddress(byte mac[]) {
  //for (int i = 5; i >= 0; i--) {
    //if (mac[i] < 16) {
      //Serial.print("0");
    //}
    //Serial.print(mac[i], HEX);
    //if (i > 0) {
      //Serial.print(":");
    //}
  //}
  //Serial.println();
//}

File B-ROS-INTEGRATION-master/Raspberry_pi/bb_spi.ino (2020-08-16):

#include <SPI.h>
#include <Servo.h>

byte buf [100];
volatile byte pos;
volatile boolean process;

int servodrive = 2; //Forward
int servodrive2 = 3; //Reverse

Servo fwd;
Servo rev;

void setup (void)
{
  Serial.begin (9600);   // debugging00

  pinMode(servodrive, OUTPUT);
  pinMode(servodrive2, OUTPUT);

  fwd.attach(servodrive);
  rev.attach(servodrive2);

  // Have to send on master in, *slave out*
  pinMode(MISO, OUTPUT);

  // Turn on SPI in slave mode
  SPCR |= _BV(SPE);
  // Enable Interrupts
  SPCR |= _BV(SPIE);

  pos = 0;
  process = false;

}  // end of setup


//Interrupt to read data into a buffered array
ISR (SPI_STC_vect)
{
  byte c = SPDR;

  if (pos < sizeof buf) {
    buf [pos++] = c;

    //This if defines the number that is being looked for in the sequence to say that one data set has been retrieved
    //eg. LinX AngZ $YOURNUMBER$ LinX AngZ $YOURNUMBER$ etc
    if (pos == 4) {
      process = true;
    }
  }
}


// Main loop - wait for flag set in interrupt routine
void loop (void)
{
  if (process) {

    uint16_t finalvalx = (uint16_t) buf[0] * 256 + (uint16_t) buf[1];
    uint16_t finalvalz = (uint16_t) buf[2] * 256 + (uint16_t) buf[3];

    //Serial.println (finalvalx);
    //Serial.println (finalvalz);
    //Serial.println ("\n");

    dcmovement(finalvalx, finalvalz);

    pos = 0;
    process = false;
  }
  stopmotion();
  delay(1000);
}  // end of loop


void dcmovement(uint16_t u, uint16_t j) {

  if (u > 1500) {
    //Forward
    fwd.writeMicroseconds(1000); //Right hand wheel
    rev.writeMicroseconds(1000); //Left Hand Wheel
    //fwd.writeMicroseconds(u);
    delay(50);

  }
  if (u < 1500) {
    //Reverse
    fwd.writeMicroseconds(2000);//right wheel
    rev.writeMicroseconds(2000);//left wheel
    //fwd.writeMicroseconds(u);
    delay(50);
  }
  if (j > 1500) {
    //Turn Right
    fwd.writeMicroseconds(2000);
    rev.writeMicroseconds(1000);
    //rev.writeMicroseconds(j);
  }
  if (j < 1500) {
    //Turn Left
    fwd.writeMicroseconds(1000);
    rev.writeMicroseconds(2000);
    //rev.writeMicroseconds(j);
  }
}

void stopmotion() {
  fwd.writeMicroseconds(1500);
  rev.writeMicroseconds(1500);
}

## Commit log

2020-08-16 Add files via upload
    +CAD FOLDER
    [Arduinopart.prt, CYBER_truck_back v1.step, CYBER_truck_front v1.step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]
2020-08-16 Add files via upload
    +IDEAS/TESTING FOLDER
    [interestingCoordinates.csv, inventory-and-tests.xlsx]
